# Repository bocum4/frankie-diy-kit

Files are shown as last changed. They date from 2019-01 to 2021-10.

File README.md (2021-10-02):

# frankie-diy-kit
Related hardware and building files. 

NOTA IMPORTANTE:

LIMITACIÓN DE GARANTÍA.

Este es un proyecto de dificultad media a avanzada. Se sugiere encarecidamente el previo conocimiento en el código de resistencias y otros elementos electrónicos así como experiencia soldando con cautín y soldadura de estaño. Bocuma no se responsabiliza por cualquier daño personal o material, defecto o malfunción derivada del incorrecto ensamble del kit.

Si tuviste problemas al armar tu kit y este no funciona después de haberlo ensamblado y verificado la guia de ensamble y guía de usuario, podremos asesorarte sin costo siempre y cuando esta revisión se realice durante los 30 días naturales siguientes a la fecha de tu compra. Transcurrido este lapso de tiempo las revisiones incurren en honorarios y están sujetas a nuestra disponibilidad y según nuestra carga de trabajo. Ponte en contacto con nosotros en contacto@bocuma.mx 

Todos nuestros kits están garantizados por nuestros proveedores, si por alguna razón algún componente de tu kit presenta una falla de fábrica lo reemplazaremos sin costo, para ello requeriremos que nos envies el componente o pieza defectuosa. Esta garantía tiene validez hasta por 3 meses después de la fecha de tu compra. Ponte en contacto con nosotros en contacto@bocuma.mx y te guiaremos en el proceso.

En caso de que a tu kit le falte una pieza o la hayas extraviado, puedes contactarnos en contacto@bocuma.mx y con gusto nos pondremos de acuerdo contigo para su reposición. Esta garantía tiene validez hasta por 3 meses después de la fecha de tu compra.

HACIA NUEVOS UNIVERSOS SONOROS | BOCUMA GDL MX 2021.

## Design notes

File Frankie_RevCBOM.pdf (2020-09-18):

Can | Valor | Designadores

SWITCHES

1 | DIP-08-PTH | MAD_SEQUENCES
8 | Switch Tactile 12mm | S1, S2, S3, S4, S5, S6, S7, S8
2 | Switch Slide | FILTER, SEQUENCER

CAPACITORES

2 | 4.7uF | C3, C5
1 | 2.2uF | C2
1 | 10uF | C7
2 | 1000pF / .001uF | C4, C6
1 | 0.22uF | C1

POTENCIOMETROS

1 | 100k (lin) | VR1
9 | 50k (lin) / 100k (lin) | F1, F2, F3, F4, F5, F6, F7, F8, PWM

RESISTENCIAS

2 | Photoresistor | R19, R20
1 | 4.7K | R14
12 | 10K | R5, R21, R22, R25, R27, R28, R29, R30, R31, R32, R33, R34
6 | 22K | R3, R8, R12, R16, R17, R26
4 | 47K | R4, R9, R13, R15
8 | 100k | R1, R2, R6, R7, R11, R23, R24, R35
1 | 390K | R18
1 | 470K | R10

CHIPS

1 | 40106N | IC6
1 | 4040N | IC7
1 | 4051N | IC8
8 | 2N3906 | Q1, Q2, Q3, Q4, Q5, Q6, Q7, Q8
5 | LM358N | IC1, IC2, IC3, IC4, IC5

HARDWARE Y OTROS MATERIALES
1 | Output jack | J1
1 | Broche bat 9V | POWER
1 | Base 14
2 | Base 16
5 | Base 8
1 | PCB Frankie

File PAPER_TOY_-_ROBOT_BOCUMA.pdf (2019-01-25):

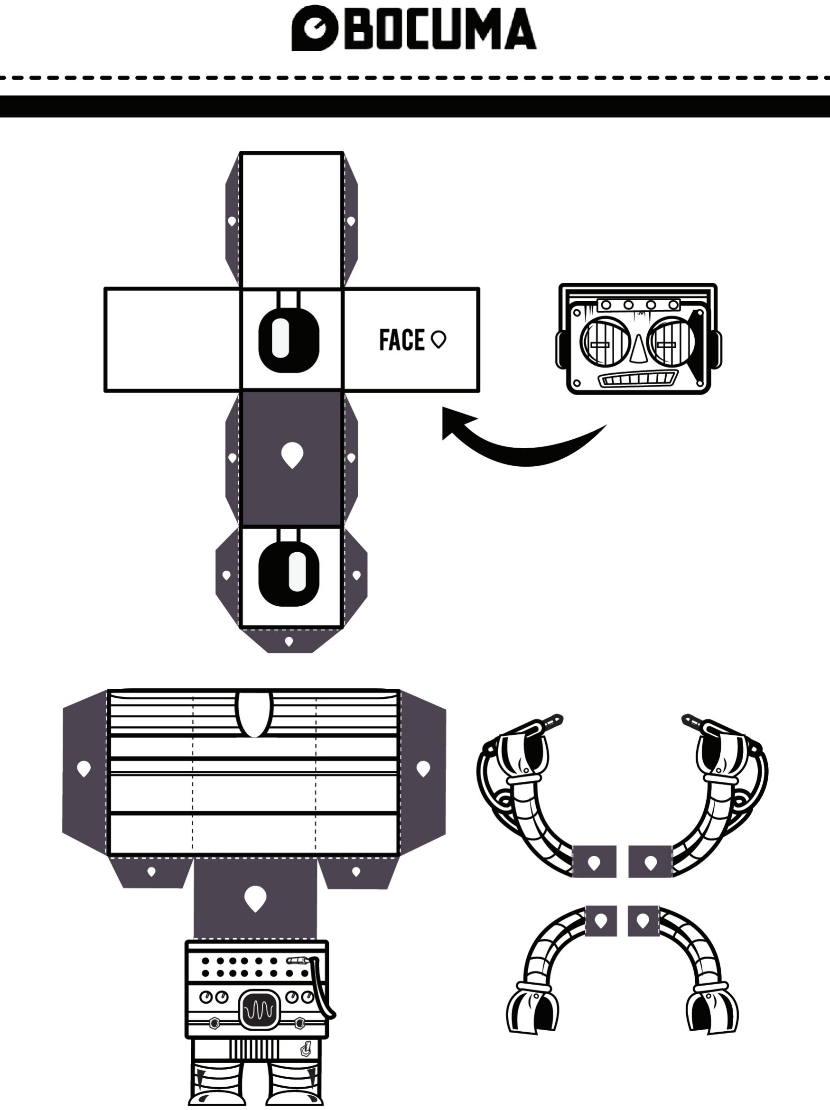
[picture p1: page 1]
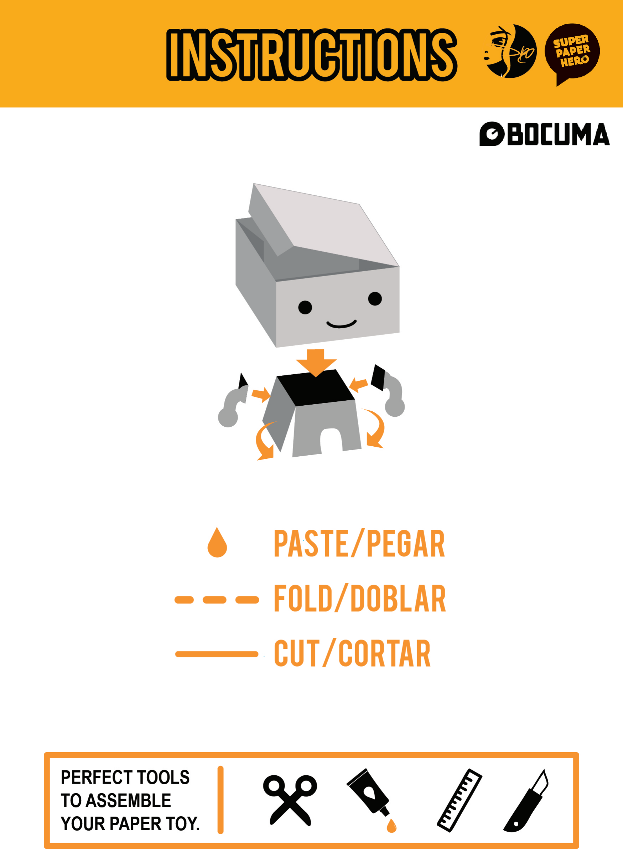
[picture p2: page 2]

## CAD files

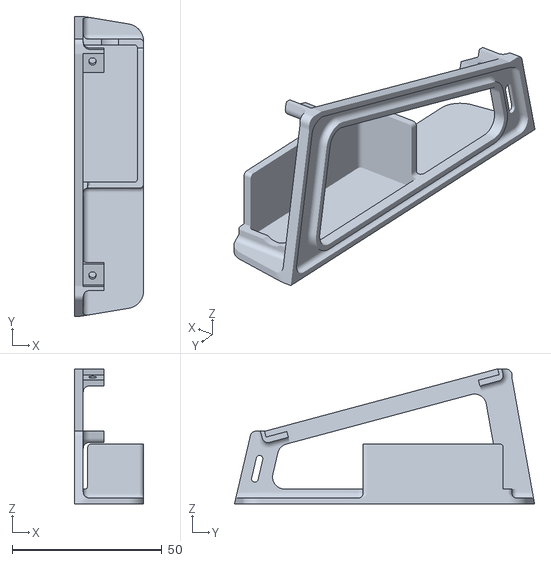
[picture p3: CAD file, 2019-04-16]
FrankieP1.stl
23.2 x 100.3 x 45.1

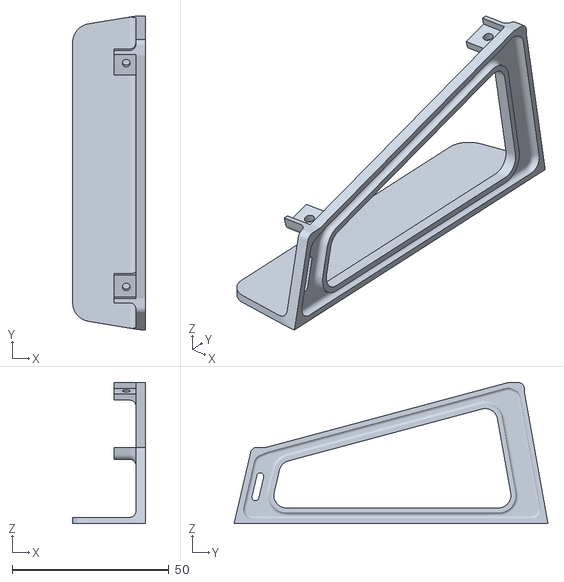
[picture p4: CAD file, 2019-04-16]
FrankieP2.stl
23.2 x 100.3 x 45.1

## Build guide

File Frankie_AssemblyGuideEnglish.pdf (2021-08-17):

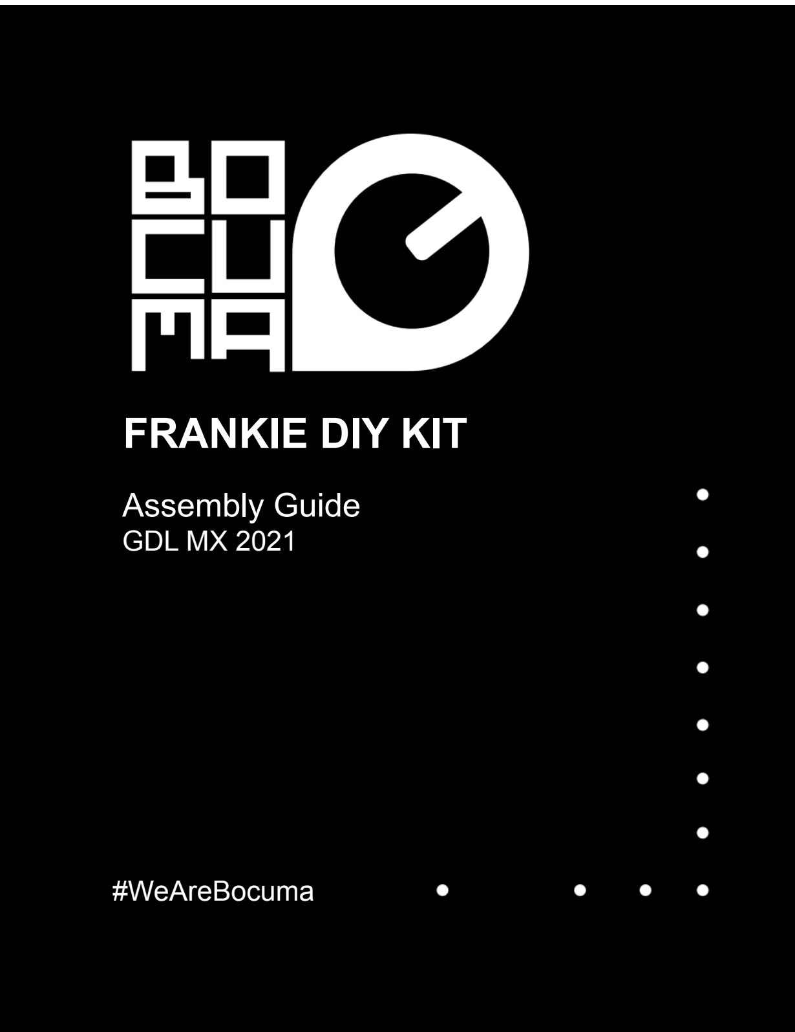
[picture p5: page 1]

# FRANKIE DIY KIT

## Assembly Guide

### GDL MX 2021

### #WeAreBocuma

## IMPORTANT NOTE

This is a medium to advanced difficulty project. Previous knowledge in the code of resistors and other electronic elements as well as experience soldering with soldering iron and tin solder is suggested. Bocuma is not responsible for any personal or material damage, defect or malfunction derived from the incorrect assembly of the kit.

TOWARDS NEW UNIVERSES OF SOUND GDL MX 2021

A few months ago, inspired by Mary Shelley's famous novel, we created Frankie. A mini beast with a sawtooth-like roar and the ability to alter his shriek with a low-pass filter, controlled by movement through the variation of light captured by a set of photoresistors.

Frankie for us was an adventure, a combination of many things learned and many things bumpy. It brought us (and still brings us) a lot of pride and we consider it as a kind of manifesto to our humble but visionary (sometimes utopian) beginnings. As in the novel, there came a point where we wanted to kill it, to stop doing it and move on to things we considered more interesting. We didn't succeed, the beast always came back, in one way or another.

At the beginning of this year, we decided to publish Frankie under a CC license and in the form of a DIY kit, because we want every individual with the necessary interest and patience to glimpse the mysteries of analog synthesis and awaken or feed his inner genius. In addition to respecting the license, we only ask that the assembly of our kit be done with passion, pride and infinite curiosity.

This is our way of giving a gift to the world.

We suggest that the user takes ownership, at least temporarily, of a clean, well-lit and well-ventilated work space. It will be necessary to gather the necessary tools and make sure to have everything ready and at hand, so that the assembly flows in a continuous and enjoyable way. For the assembly it is required:

× Pencil soldering iron, with a point in good condition. × Soldering wire as needed
× Cutting tweezers.
× Pointed tweezers.
× Desoldering and the cunning to use it very little (or not at all).

To this list we could add patience, curiosity and all those elements that make the assembly more bearable. We like to drink coffee and assemble at night. Occasional night work allows for some inspiration that also gets from the quiet and mystery of the wee hours of the morning. The above strikes us as very ad-hoc to Frankie's monstrous subject matter. As for the ears, we like to embellish the silence of the studio-workshop with good music, the selection of which we leave to the user's discretion.

It is essential to be confident with the soldering iron and to have experience in the art of soldering PTH components, as well as knowing how to identify electronic elements and resistor values.

With everything said here, assembling the kit should not present any mishap and we hope that the user enjoys assembling it as much as we enjoyed the process of designing it.

## BOM AND PCB

Before starting, we will have to familiarize ourselves with the necessary components for the assembly, it will be necessary to review the BOM (bill of materials) in the following link:
- click here- (https://github.com/bocum4/frankie-diy-kit)Next we must familiarize ourselves with the PCB layout (electronic board):

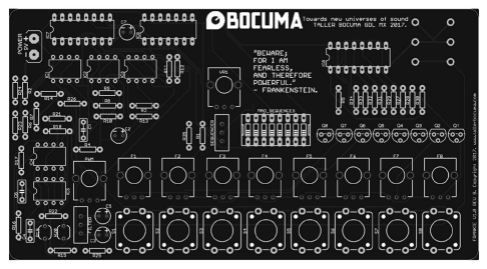
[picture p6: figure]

Each component on the board has its identifier and corresponding silhouette printed on it. All elements (with the exception of the audio output connector) are positioned on this side of the PCB.

## ASSEMBLY

Without further ado.
We begin by inspecting the electronic board to

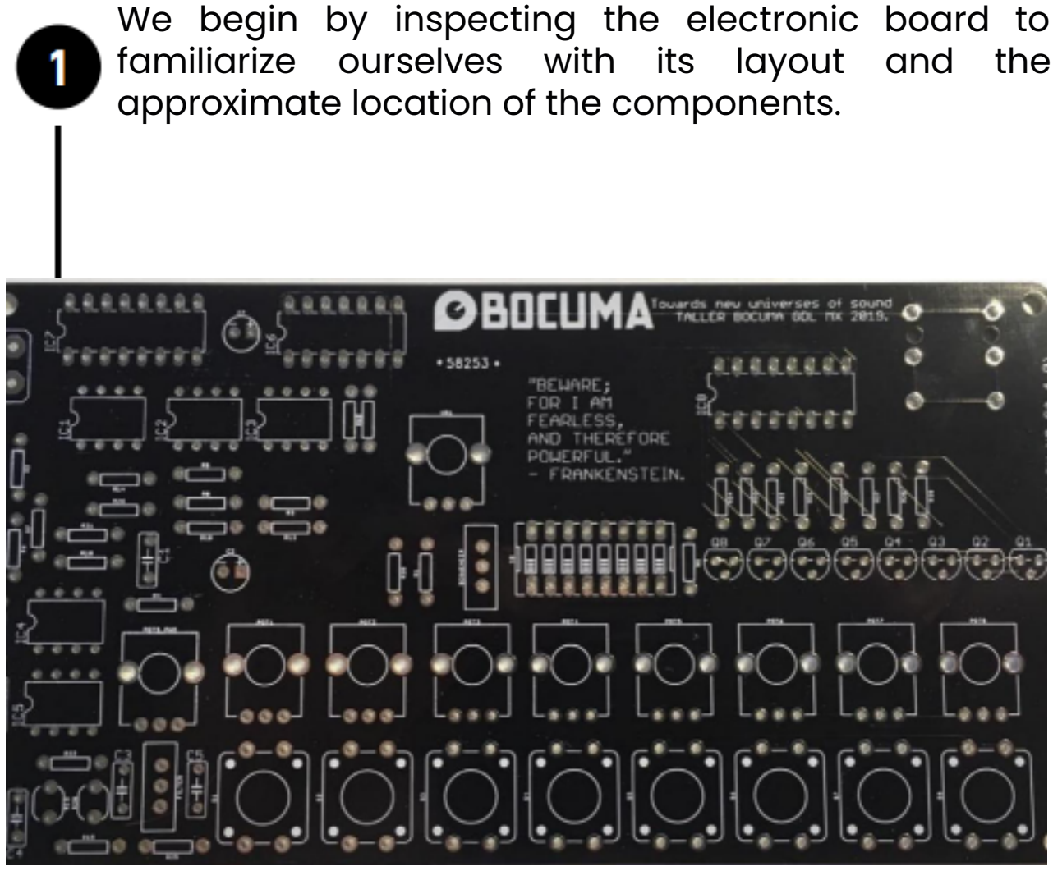
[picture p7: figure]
approximate location of the components.

familiarize ourselves with its layout and the

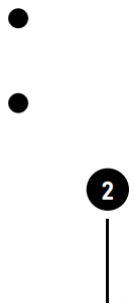
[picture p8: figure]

We start by soldering the resistors, referring to their value on the parts list value in the parts list and finding the location of each one on the board:

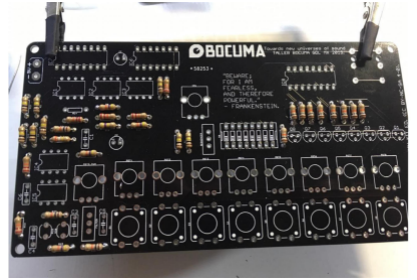
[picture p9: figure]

In the case of resistors, they do not have polarity, so it does not matter which way they are soldered. However, we must pay attention to their color code and place the indicated values in the corresponding place.

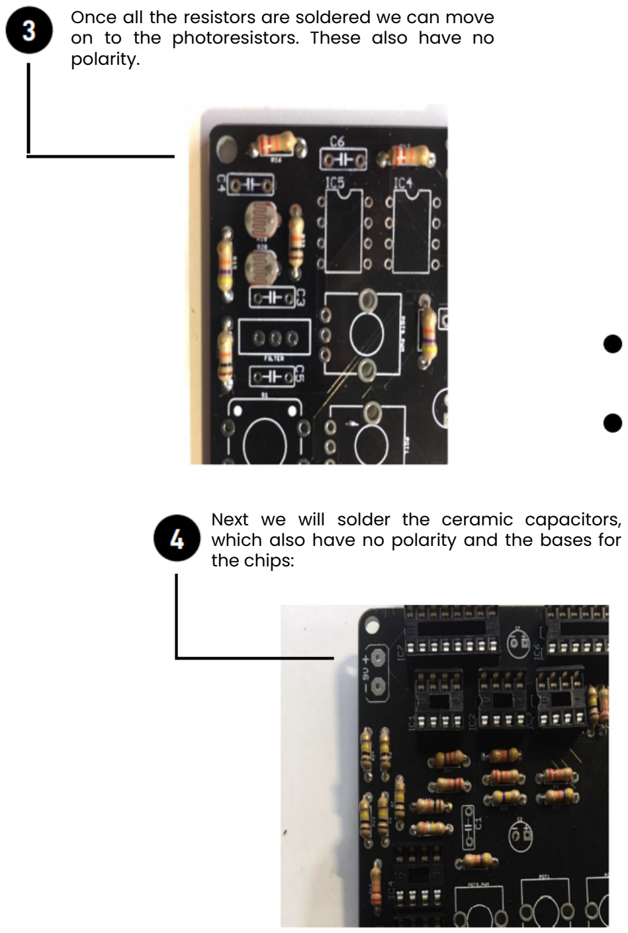
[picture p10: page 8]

Once all the resistors are soldered we can move on to the photoresistors. These also have no polarity.

Next we will solder the ceramic capacitors, which also have no polarity and the bases for the chips:

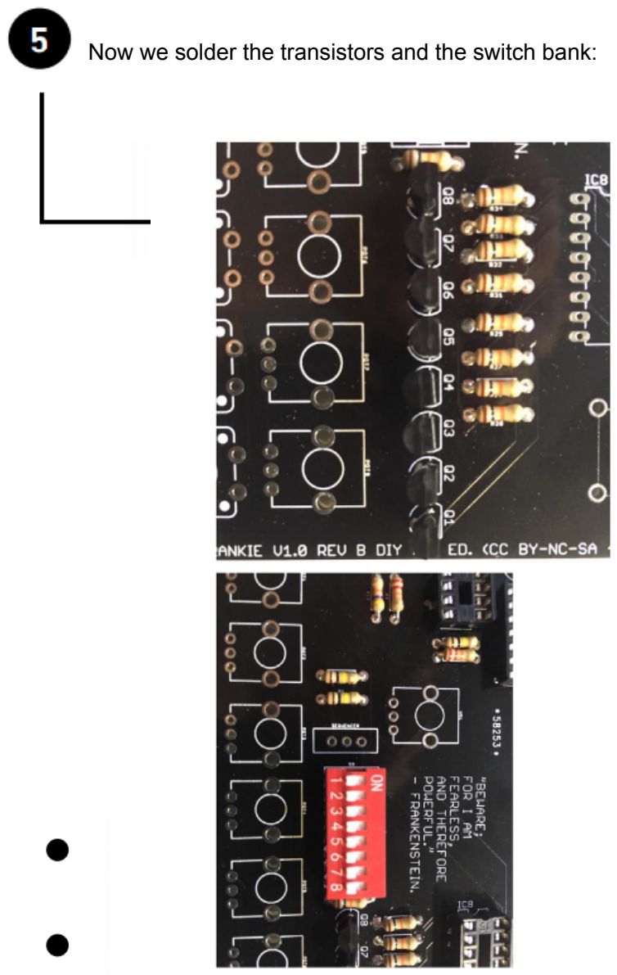
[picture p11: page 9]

5

Now we solder the transistors and the switch bank:

We continue with the electrolytic capacitors paying close attention to their POLARITY and their value, remembering that the gray stripe on the capacitor must go in the hole marked with a negative symbol (-).

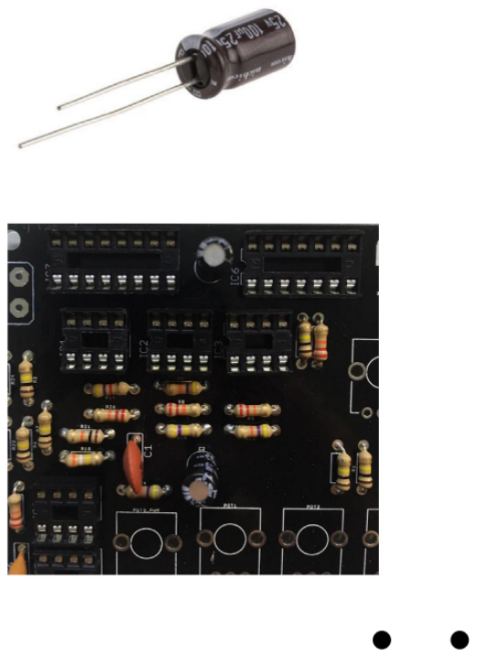
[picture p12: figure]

Now we will take care of the pulse buttons and the sequencer and filter switches:

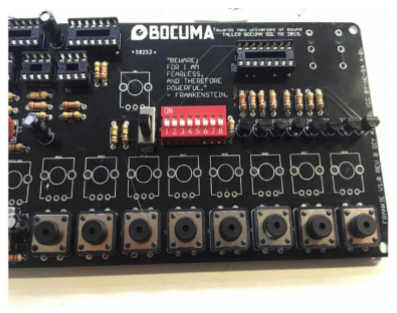
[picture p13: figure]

For the sequencer switches and the filter, we will have to cut the two end plates with tweezers.

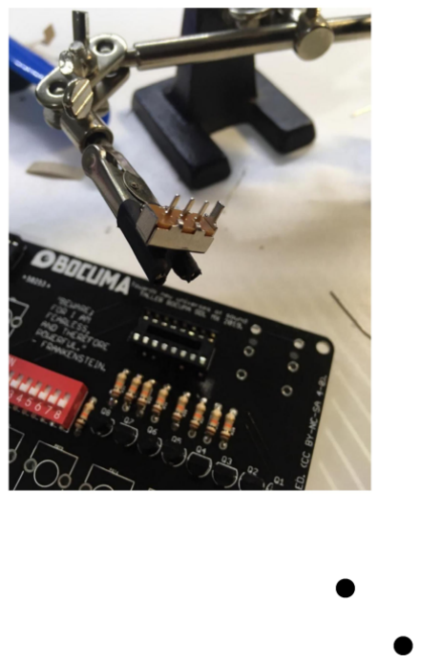
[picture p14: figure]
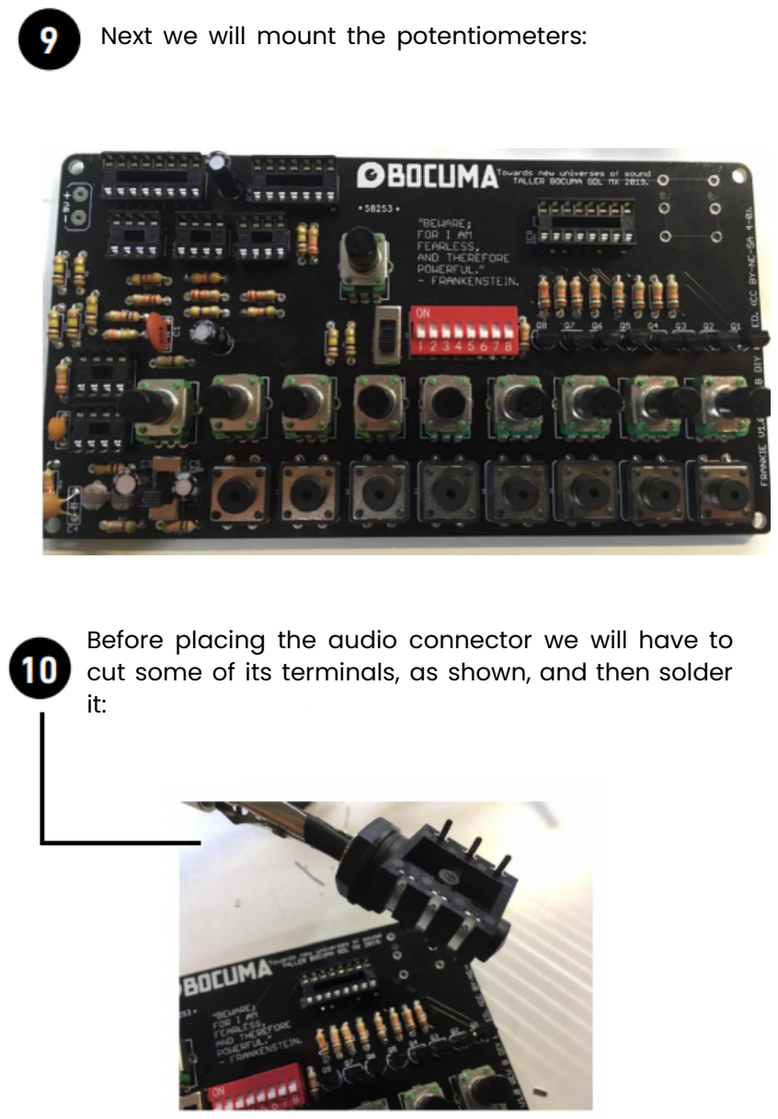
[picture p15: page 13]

Next we will mount the potentiometers:ll mount

### the potentiometers:

Before placing the audio connector we will have to cut some of its terminals, as shown, and then solder it:

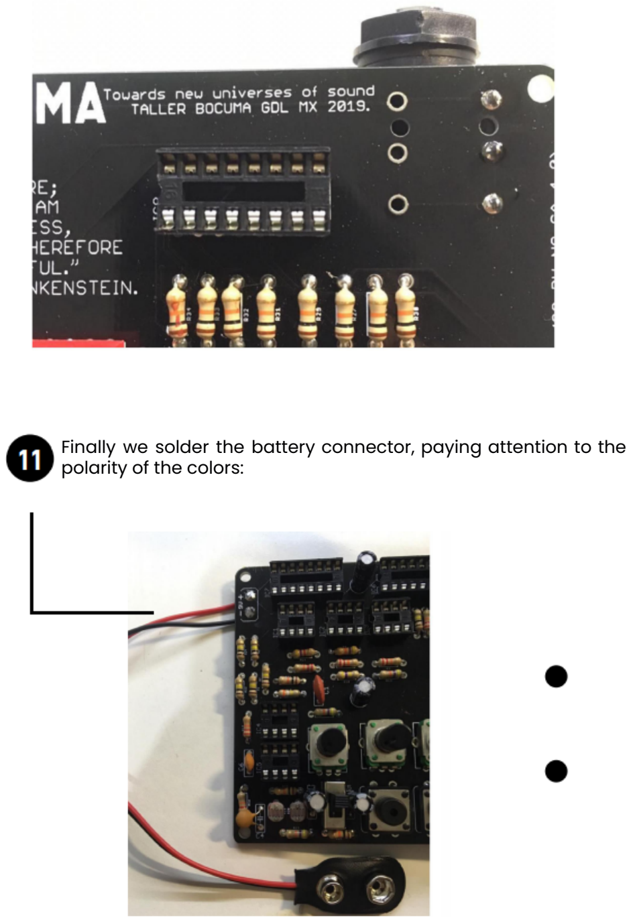
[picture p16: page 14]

Fin

ally

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
## ¿IS IT ALIVE?

To make Frankie emit his first roars, you only need to connect a 9V battery, we recommend buying a rechargeable battery to save the economy and the planet. It would be a good idea to consult the instructions here:

click here (https://github.com/bocum4/frankie-diy-kit)

DALE CLICK

## Assembly Guide

## GDL MX 2021

## #WeAreBocuma

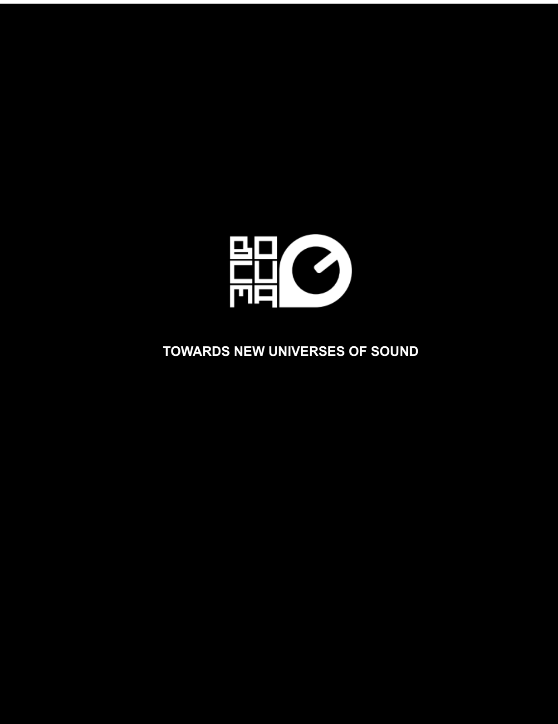
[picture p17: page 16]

TOWARDS NEW UNIVERSES OF SOUND

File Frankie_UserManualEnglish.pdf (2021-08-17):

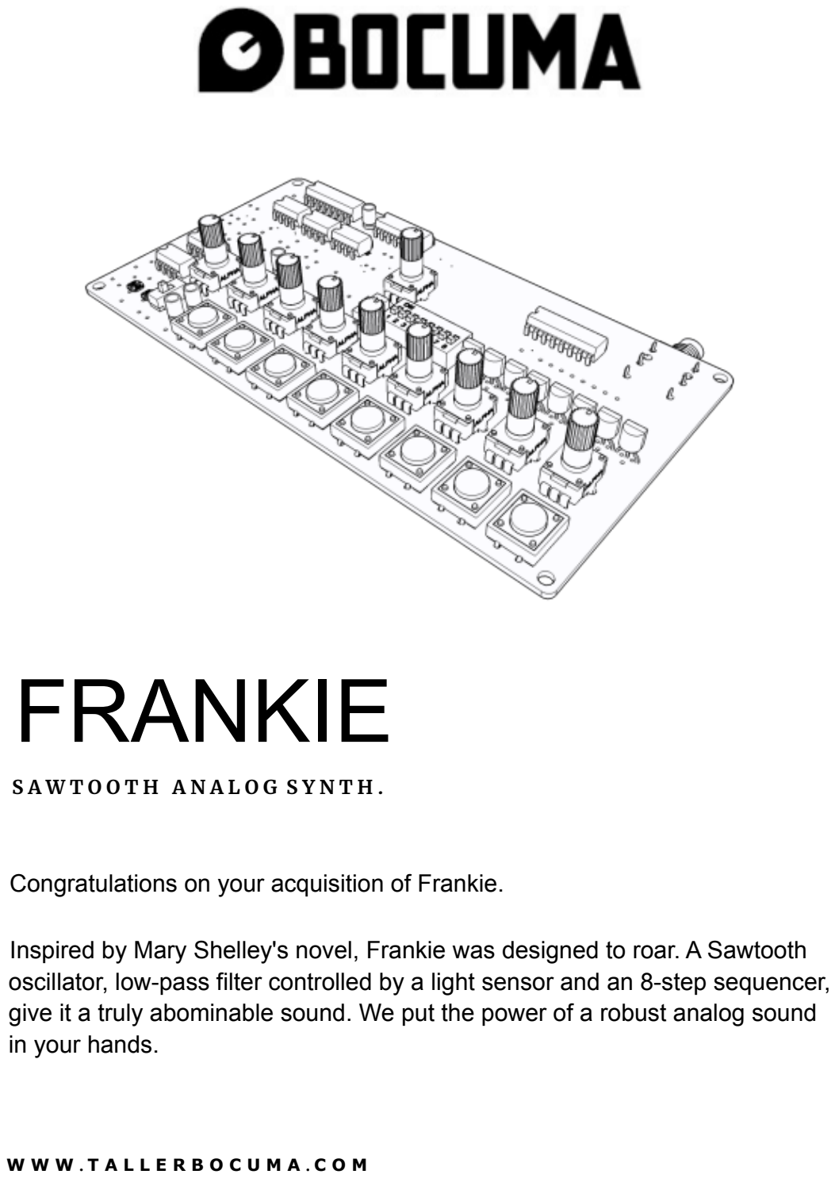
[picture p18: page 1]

# FRANKIE

S A W T O O T H A N A L O G S Y N T H .

Congratulations on your acquisition of Frankie.

### Inspired by Mary Shelley's novel, Frankie was designed to roar. A Sawtooth

oscillator, low-pass filter controlled by a light sensor and an 8-step sequencer,

### give it a truly abominable sound. We put the power of a robust analog sound

in your hands.

W W W . T A L L E R B O C U M A . C O M

D I S T R I B U T I O N O F T H E C O M P O N E N T S:

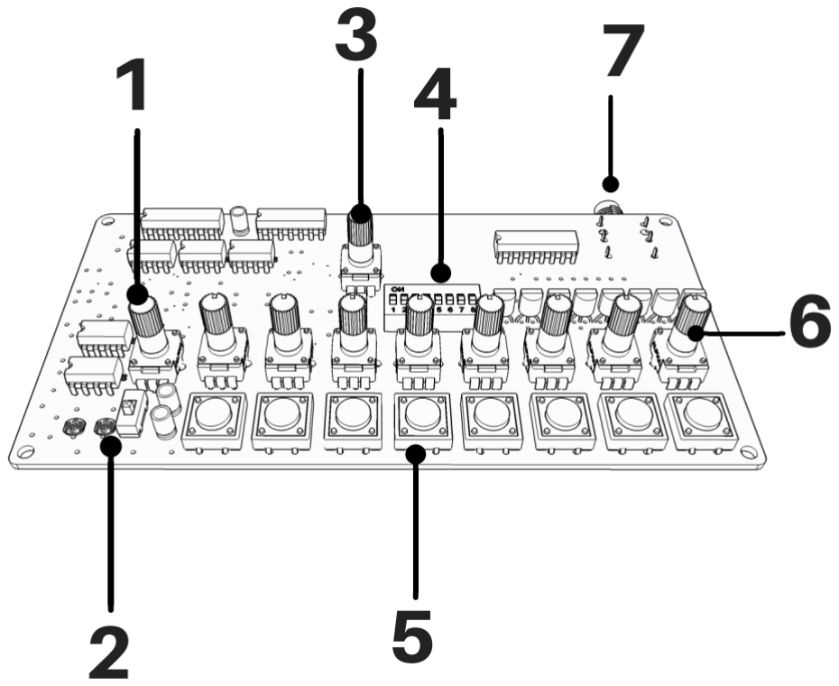
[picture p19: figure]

1. Pitch adjustment (PWM).
2. Switch and filter sensor.
3. Switch and sequencer rate (the switch is under the knob).
4. Sequence bank.
5. Note buttons (trigger).
6. Note setting (frequency).
7. Audio output.

M A N U A L O P E R A T I O N (S E Q U E N C E R D E A C T I V A T E D):

A. Connect a 9v battery to Frankie's power connector and its audio output (7) to an amplifier.
B. Set the first three sequence bank switches (4) to the "ON" (up) position, the speed or rate knob (3) all the way to the left and the switch below it all the way down (OFF).
C. To adjust Frankie's initial frequency pitch, set the "pitch adjustment" knob (1) to halfway. This knob must be held in this position in order to generate a signal at the output. You can experiment slightly to change Frankie's overall tone.
D. Press and hold any of the eight knobs (5) and then adjust its note with the knob (6) immediately above it, until it is to your liking. Each button can be set to play a different note when pressed.
E. To activate the filter, simply turn the filter switch (2) to its ON position. The filter cutoff frequency is controlled by the light level detected in the sensor (2). While pressing a note (5), move your hand closer and further away to listen to the results.

S E Q U E N C E R O P E R A T I O N:

A. With the first 3 sequence bank switches (4) facing up (ON) , set the sequencer switch under the rate knob (3) also facing up (ON). With this setting, Frankie will play its 8 notes in a linear fashion from left to right,
B. Increase the speed of the sequence (rate) by moving the knob (3) gradually to the right.
C. To change the sequence activation order, experiment with different combinations with the sequence bank switches (4).
D. To activate the filter, simply position the filter switch (2) upwards to its ON position. The filter cutoff frequency is controlled by the light level detected in the sensor (2). While the sequences are playing, move your hand closer and further away to listen to the results.

This tutorial is only a guide for initial use, the possibilities are vast. We designed Frankie with exploration in mind and hope you enjoy your experiments as much as we enjoyed designing and assembling it.

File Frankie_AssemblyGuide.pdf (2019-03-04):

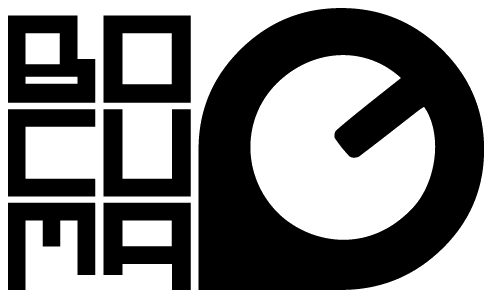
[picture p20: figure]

# FRANKIE DIY KIT

# GUÍA DE ENSAMBLE GDL MX 2019 #somosbocuma

# NOTA IMPORTANTE:

Este es un proyecto de dificultad media a avanzada. Se sugiere el previo conocimiento en el código de resistencias y otros elementos electrónicos así como experiencia soldando con cautín y soldadura de estaño. Bocuma no se responsabiliza por cualquier daño personal o material, defecto o malfunción derivada del incorrecto ensamble del kit.

HACIA NUEVOS UNIVERSOS SONOROS | BOCUMA GDL MX 2019.

# INTRO

Hace algunos meses, inspirandonos en la famosa novela de Mary Shelley, creamos a Frankie. Una mini bestia con rugido a tono diente de sierra y la capacidad de alterar su alarido con un filtro pasa-bajas, controlado por movimiento mediante la variación de luz captada por un conjunto de fotorresistores.

Frankie para nosotros fue una aventura, una combinación de muchas cosas aprendidas y muchas otras accidentadas. Nos trajo (y trae aún) mucho orgullo y lo consideramos como una especie de manifesto a nuestros humildes pero visionarios (a veces utópicos) inicios. Al igual que en la novela, llegó el punto donde quisimos matarlo, dejar de hacerlo y pasar a cosas que considerábamos más interesantes. No lo logramos, la bestia siempre volvió, de alguna manera u otra.

A inicios de este año, decidimos publicar a Frankie bajo una licencia CC y en forma de kit DIY, por que queremos que todo individuo con el interés y la paciencia necesaria, pueda vislumbrar los misterios de la sintesis analogica y despierte o alimente a su genio interior. Además del respeto a la licencia, solo pedimos que el ensamble de nuestro kit se realice con pasión, orgullo e infinita curiosidad.

Esta es nuestra manera de darle un regalo al mundo.

# ANTES DE COMENZAR

Sugerimos que el usuario se apropie, al menos de manera temporal, de un espacio de trabajo limpio, bien iluminado y bien ventilado. Habrá que reunir las herramientas necesarias y asegurarse de tener todo listo y a la mano, de tal manera que el ensamble fluya de manera continua y disfrutable. Para el ensamble se requiere:

- Cautín de lapíz, con una punta en buen estado.
- Soldadura al gusto.
- Pinzas de corte.
- Pinzas de punta.
- Desoldador y la astucia para usarlo muy poco (o nada).

A esta lista podríamos añadir la paciencia, la curiosidad y todos aquellos elementos que hagan del ensamble más llevadero. A nosotros nos gusta beber café y ensamblar durante la noche. El ocasional trabajo noctámbulo permite cierta inspiración que solo obtenemos de la tranquilidad y misterio de las altas horas de la madrugada. Lo anterior nos parece muy ad-hoc a la monstruosa temática de Frankie. En cuanto a las orejas, nos gusta adornar el silencio del estudio-taller con buena música cuya selección dejaremos al criterio del usuario.

Es esencial tener confianza en la maniobra del cautín y contar con experiencia en el arte de la soldadura con estaño para componentes PTH, así como saber identificar elementos electrónicos y valores de resistencias.

Con todo lo dicho aquí, ensamblar el kit no debe presentar ningún percance y esperamos que el usuario disfrute de ensamblarlo tanto como nosotros disfrutamos el proceso de diseñarlo.

# BOM Y PCB

Antes de comenzar, tendremos que familiarizarnos con los componentes necesarios para el ensamble, será necesario revisar el BOM (lista de materiales) en la siguiente
liga: | https://github.com/TBocuma/frankie-diy-kit/blob/master/Frankie_BOM.pdf | para
después identificarlos en el contenido del kit.

A continuación debemos familiarizarnos con el layout del PCB (tarjeta electrónica):

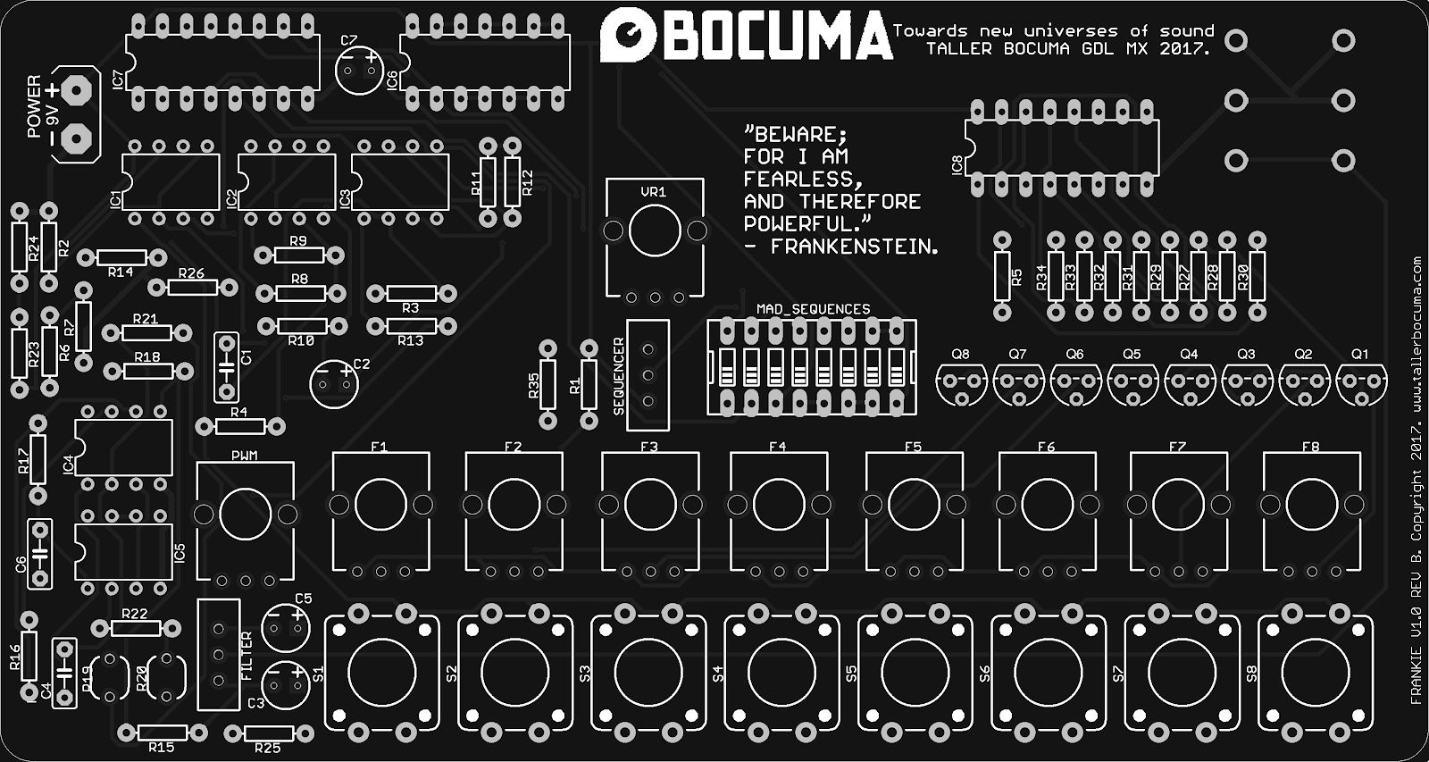
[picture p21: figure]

Cada componente en la tarjeta tiene impreso su identificador y su silueta correspondiente. Todos los elementos (a excepción del conector de salida de audio) se posicionan en esta cara del PCB.

# ENSAMBLE

Sin mayor preámbulo.

1) Iniciamos inspeccionando la tarjeta electrónica para familiarizarnos con su layout y la ubicación aproximada de los componentes.

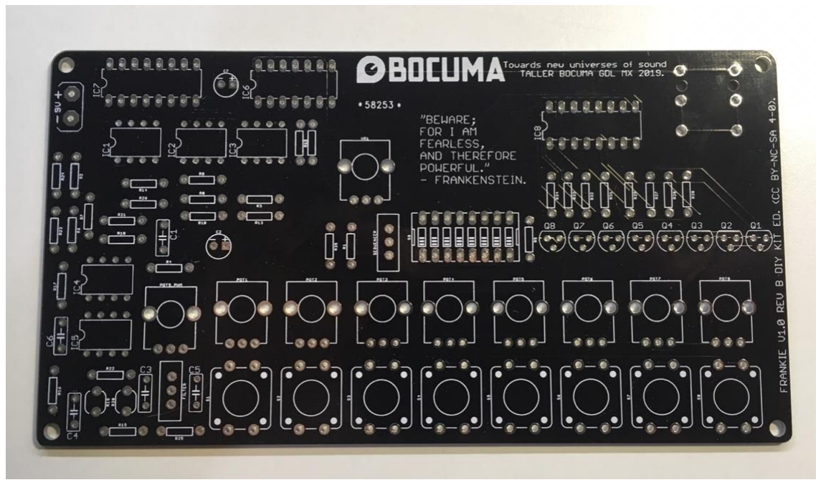
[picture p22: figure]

2) Iniciamos soldando las resistencias, refiriéndonos a su valor en la lista de partes y buscando la ubicación de cada una en la tarjeta:

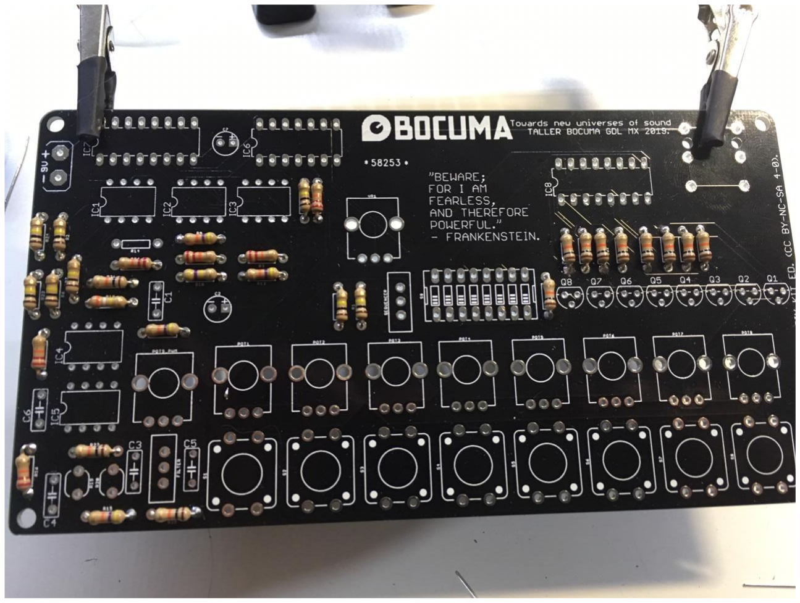
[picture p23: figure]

En el caso de las resistencias, no presentan polaridad por lo que no importa con qué orientación las soldemos. Sin embargo, hay que prestar atención a su código de colores y colocar los valores indicados en el lugar correspondiente.

3) Una vez soldadas todas las resistencias podemos pasar a los fotoresistores. Estos tampoco presentan polaridad.

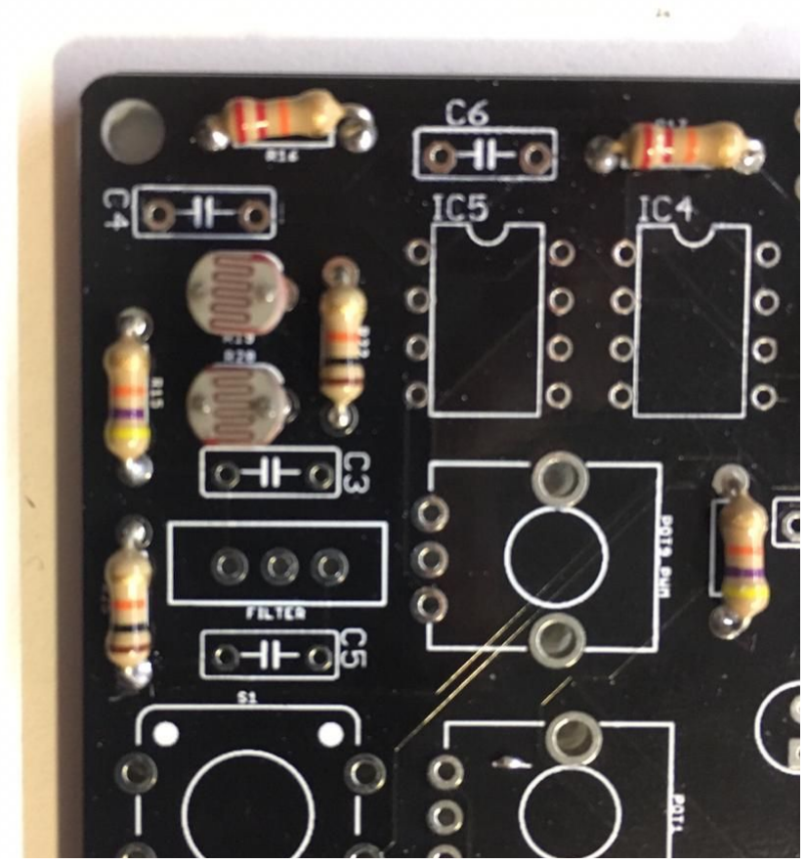
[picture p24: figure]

3) A continuación soldaremos los capacitores ceramicos, que tampoco presentan polaridad y las bases para los chips:

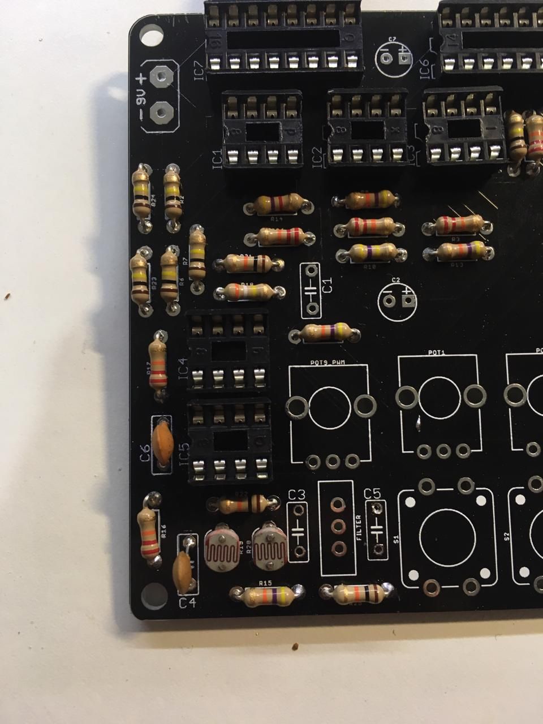
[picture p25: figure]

6) Ahora soldamos los transistores y el banco de switches:

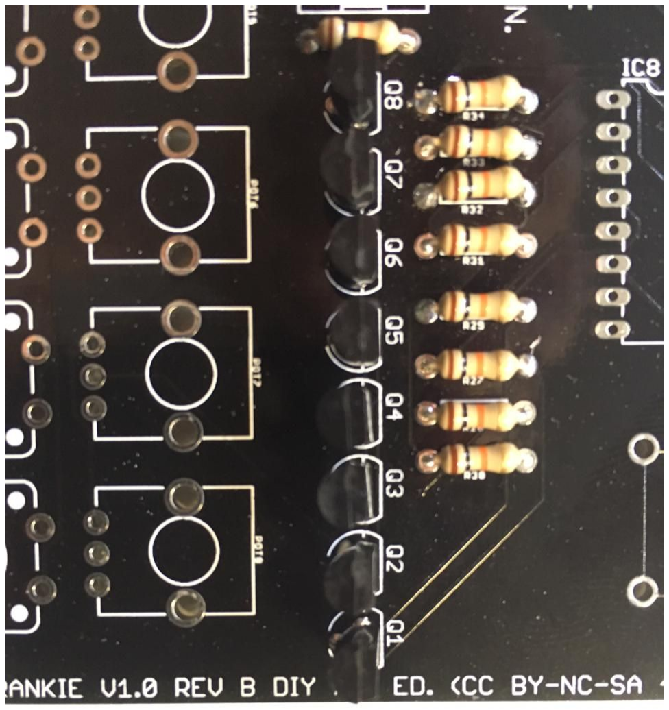
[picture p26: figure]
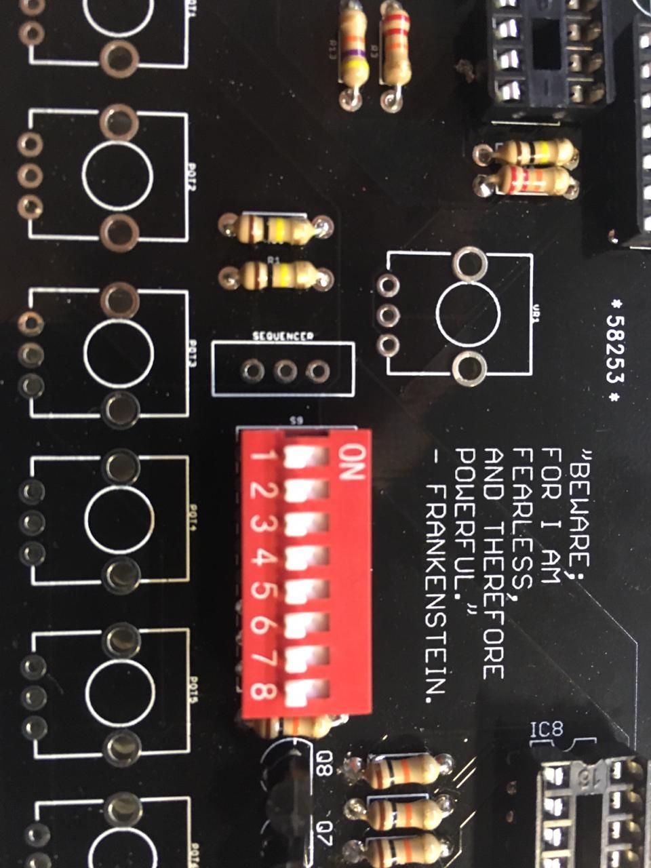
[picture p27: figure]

5) Continuamos con los capacitores electrolíticos poniendo mucha atención en su POLARIDAD y su valor, recordando que la franja gris en el capacitor debe ir en el orificio marcado con un símbolo negativo (-).

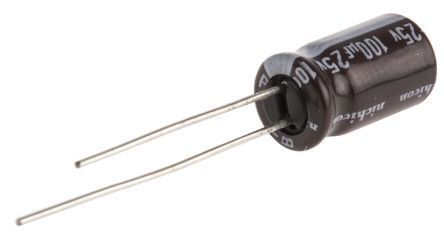
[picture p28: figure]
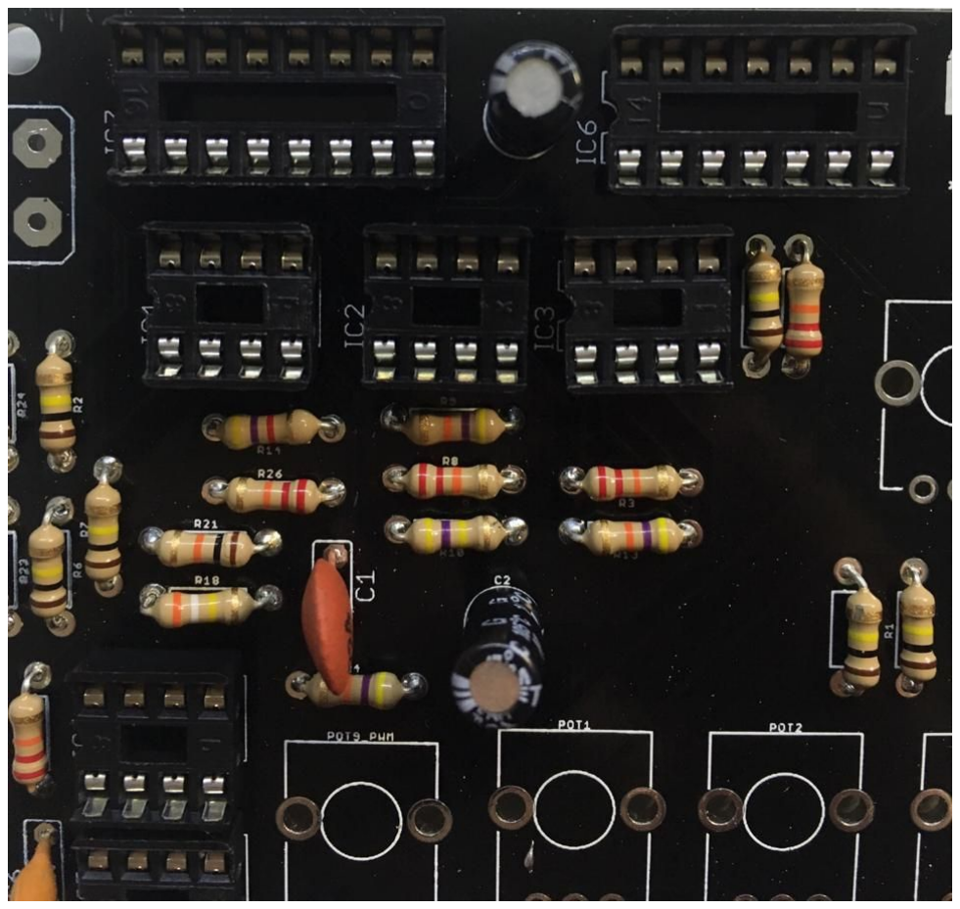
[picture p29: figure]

6) Ahora nos haremos cargo de los botones de pulso y los switches del secuenciador y el filtro:

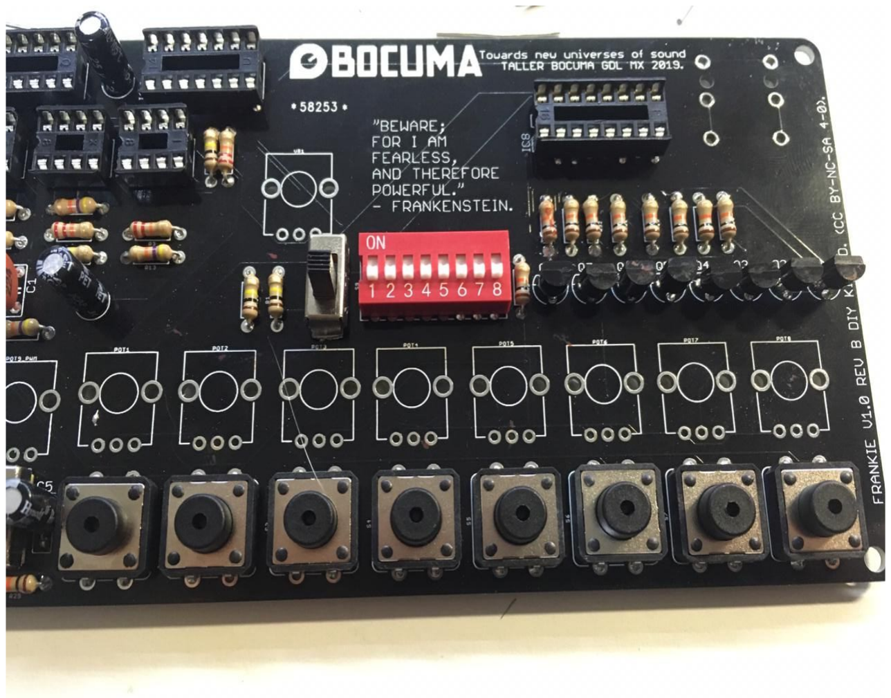
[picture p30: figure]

Para los interruptores del secuenciador y el filtro, tendremos que cortar las dos láminas de los extremos con unas pinzas.

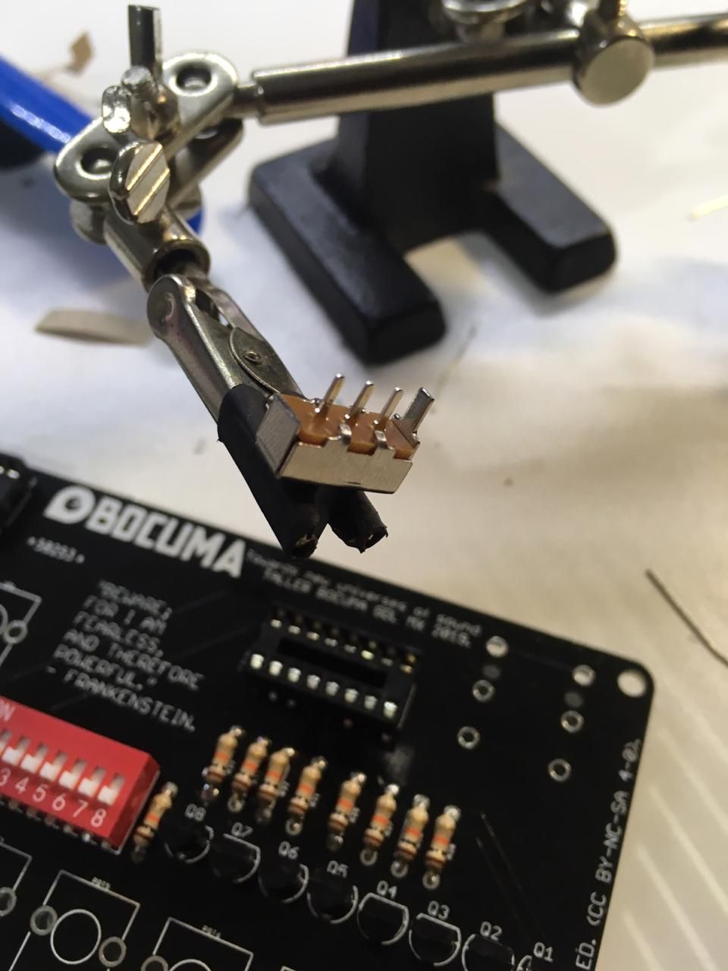
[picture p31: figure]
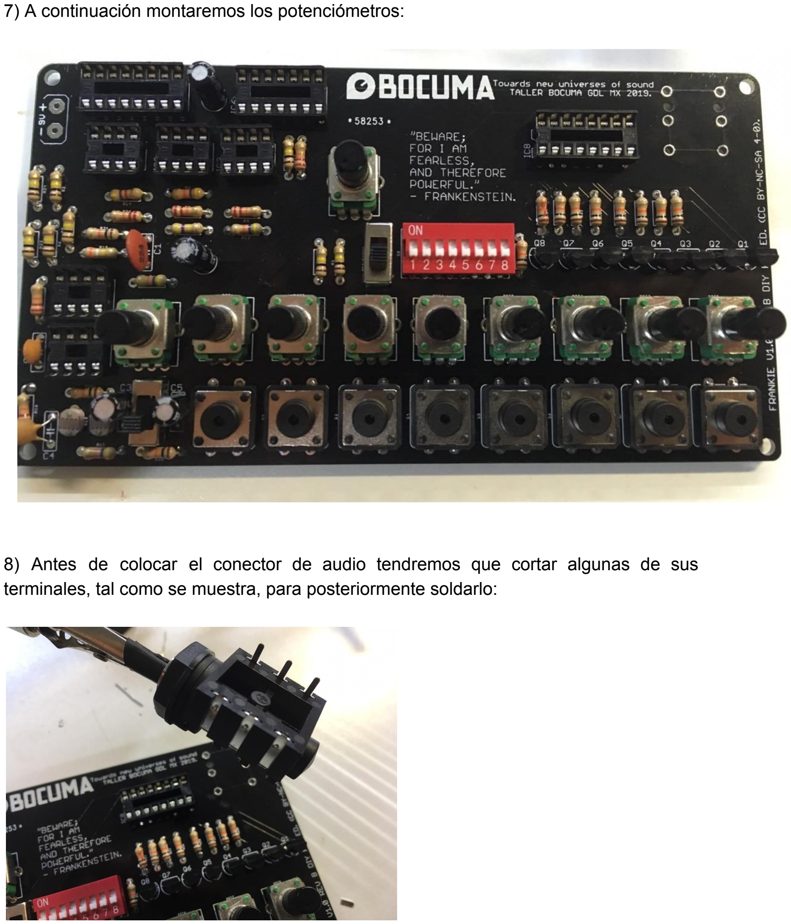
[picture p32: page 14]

7) A continuación montaremos los potenciómetros:
8) Antes de colocar el conector de audio tendremos que cortar algunas de sus terminales, tal como se muestra, para posteriormente soldarlo:

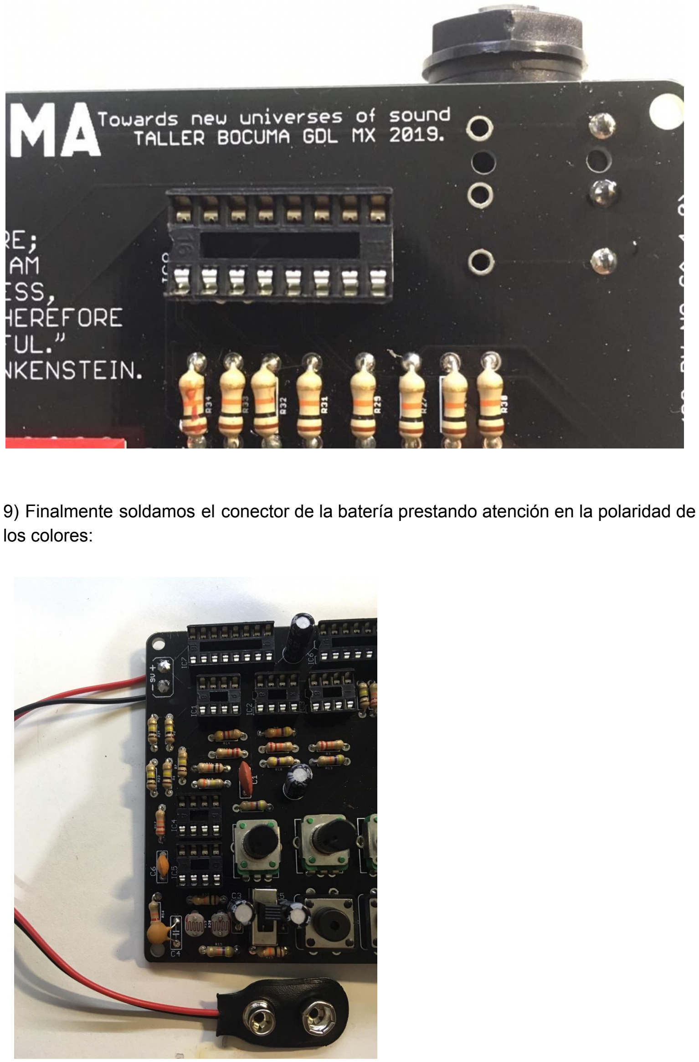
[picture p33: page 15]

9) Finalmente soldamos el conector de la batería prestando atención en la polaridad de los colores:

# ¿ESTA VIVO?

Para que Frankie emita sus primeros rugidos, solo hace falta conectarle una batería de 9V, nosotros recomendamos adquirir una batería recargable para cuidar la economía y el planeta. Vendría bien consultar el instructivo aquí:

https://github.com/TBocuma/frankie-diy-kit/blob/master/InstructivoFrankie.pdf

# #somosbocuma

Hacia nuevos universos sonoros. GDL MX.
Marzo 2019.

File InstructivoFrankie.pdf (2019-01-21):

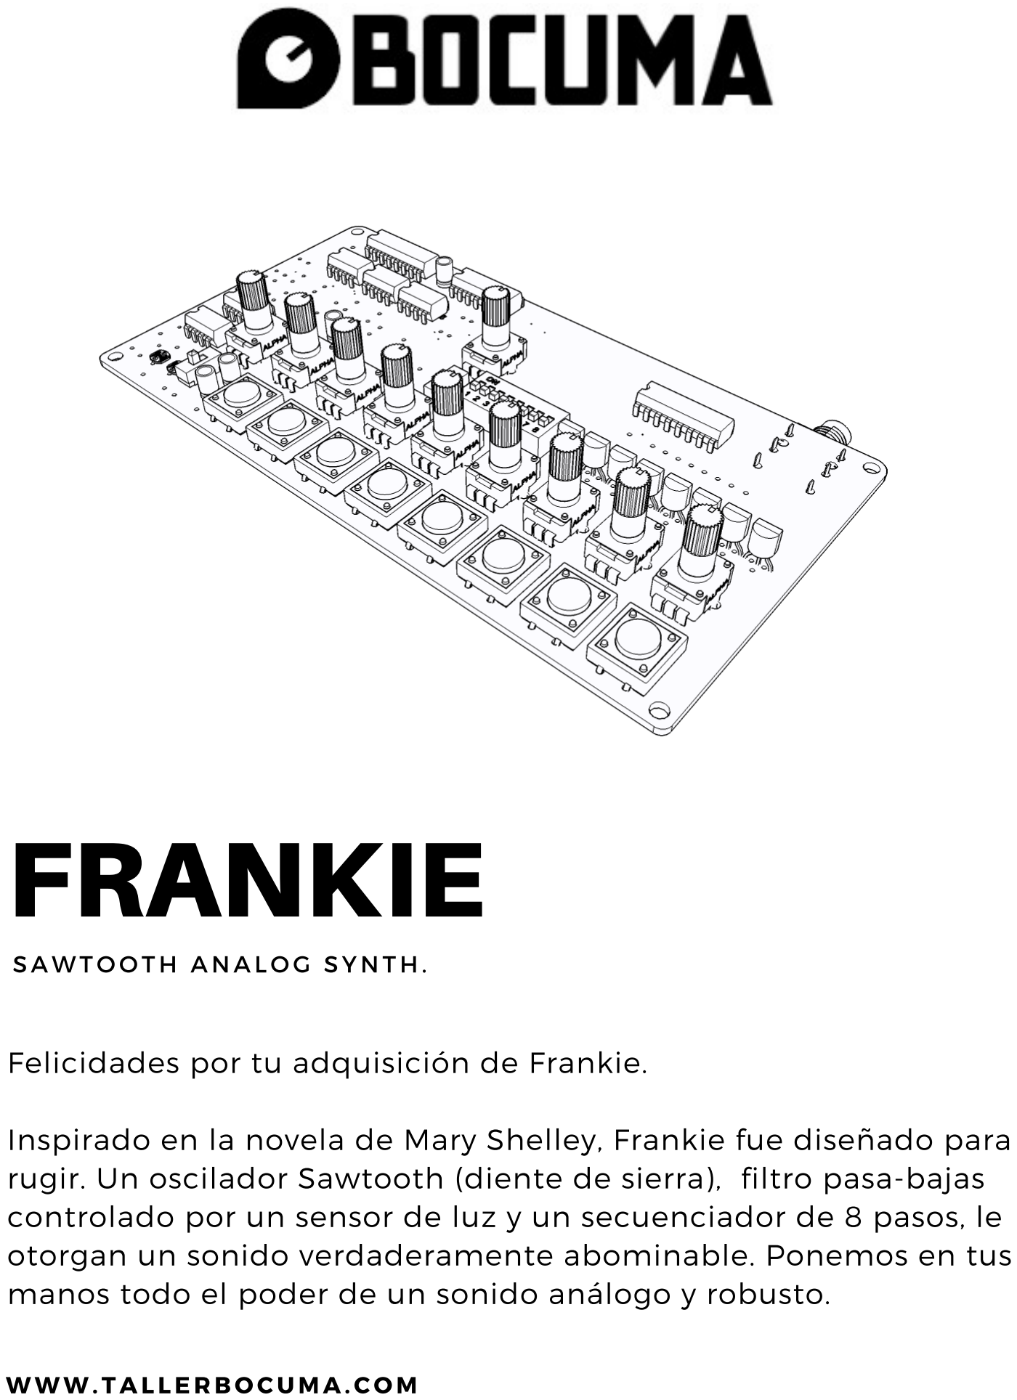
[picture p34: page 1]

S AWT O O T H A N A L O G SY N T H .

WWW. T A L LE R B O C U M A .C O M

Felicidades por tu adquisición de Frankie.

Inspirado en la novela de Mary Shelley, Frankie fue diseñado para

rugir. Un oscilador Sawtooth (diente de sierra), filtro pasa-bajas

controlado por un sensor de luz y un secuenciador de 8 pasos, le

otorgan un sonido verdaderamente abominable. Ponemos en tus

manos todo el poder de un sonido análogo y robusto.

# FRANKIE

1

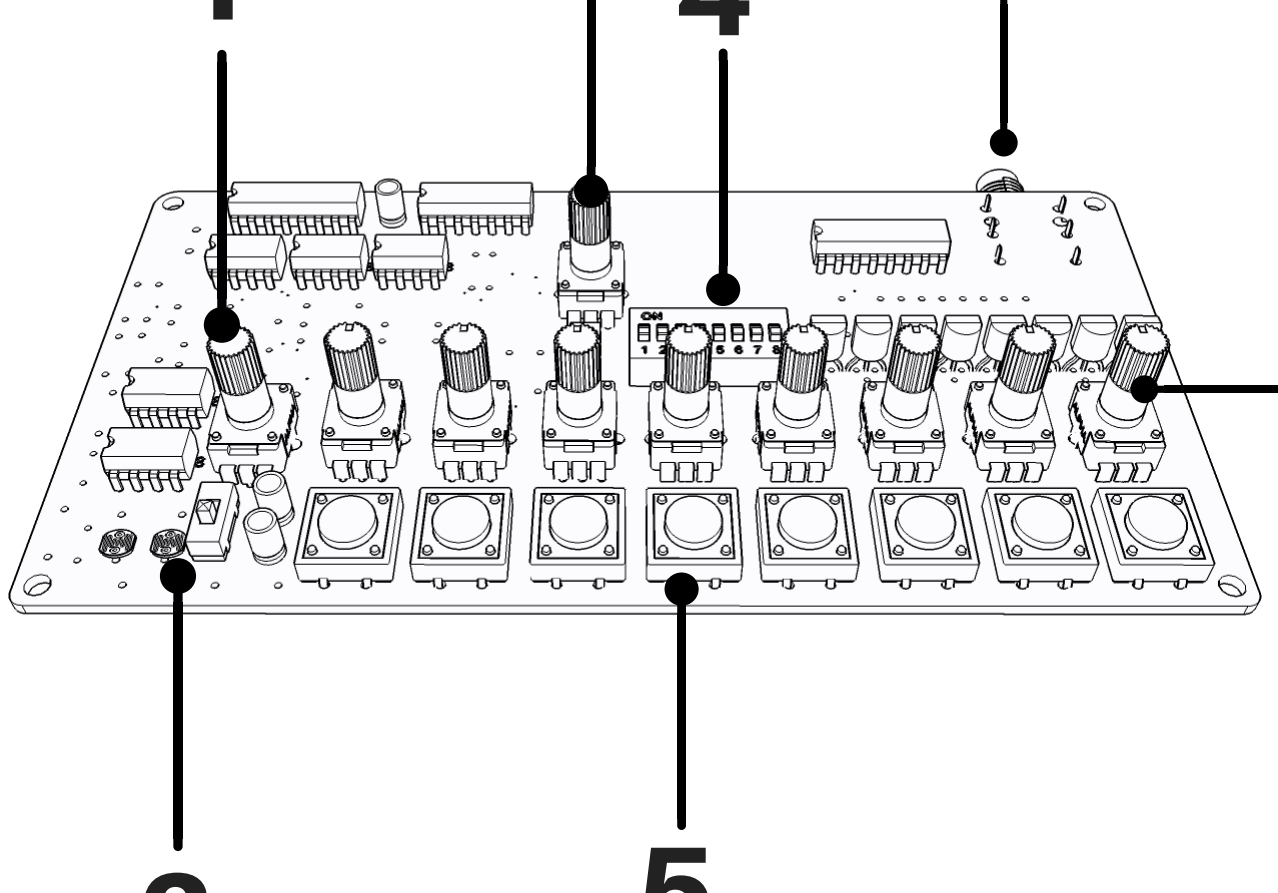
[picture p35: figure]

2

3
4

5

6

7

1. Ajuste de tono (PWM).
2. Switch y sensor del filtro.
3. Switch y velocidad (rate) del secuenciador (el switch está

debajo de la perilla).

4. Banco de secuencias.
5. Botones de nota (trigger).
6. Ajuste de nota (frecuencia).
7. Salida de Audio.

D I S T R I B U CI Ó N D E L O S C O M P O N E N TES :

O PE R A CI Ó N M A N U A L ( SEC U E N CI A D O R D ES A CT IV A D O ):

A. Conecta una batería de 9v al conector de poder de Frankie y su salida de audio
(7) a un amplificador.
B. Posiciona los tres primeros switches del banco de secuencias (4) en la posición

"ON" (arriba), la perilla de velocidad o rate (3) totalmente hacia la izquierda y el

switch debajo de esta, hacia abajo (OFF).

C. Para ajustar el tono inicial de frecuencia de Frankie, coloca la perilla de "ajuste

de tono" (1) a la mitad. Esta perilla debe mantenerse en esta posición para poder

generar una señal en la salida. Puedes experimentar ligeramente para cambiar el

tono general de Frankie.

D. Mantén presionado cualquiera de los ocho botones (5) y después ajusta su nota

con la perilla (6) inmediatamente arriba de este, hasta que sea de tu agrado. Cada

botón puede ajustarse para reproducir una nota diferente al ser presionado.

E. Para activar el filtro, simplemente posiciona el switch del filtro (2) hacia arriba, en

su posición de encendido (ON). La frecuencia de corte del filtro es controlada por el

nivel de luz detectado en el sensor (2). Mientras presionas una nota (5), acerca y

aleja tu mano para escuchar los resultados.

O PE R A CI Ó N D EL SEC U E N CI A D O R :

A. Con los primeros 3 switches del banco de secuencias (4) hacia arriba (ON) coloca

el switch del secuenciador, debajo de la perilla rate (3) también hacia arriba (ON).

Con esta configuración, frankie reproducirá sus 8 notas de manera lineal de

izquierda a derecha,

B. Incrementa la velocidad de la secuencia (rate) moviendo la perilla (3)

gradualmente hacia la derecha.

C. Para cambiar el orden de activación de la secuencia, experimenta con diferentes

combinaciones con los switches del banco de secuencias (4).

D. Para activar el filtro, simplemente posiciona el switch del filtro (2) hacia arriba,

en su posición de encendido (ON). La frecuencia de corte del filtro es controlada

por el nivel de luz detectado en el sensor (2). Mientras se reproducen las

secuencias, acerca y aleja tu mano para escuchar los resultados.

Este instructivo constituye solamente una guía de uso inicial, las

posibilidades son muy amplias. Diseñamos a Frankie con la exploración

en mente y esperamos que disfrutes tus experimentos tanto como

nosotros disfrutamos diseñarlo y ensamblarlo.

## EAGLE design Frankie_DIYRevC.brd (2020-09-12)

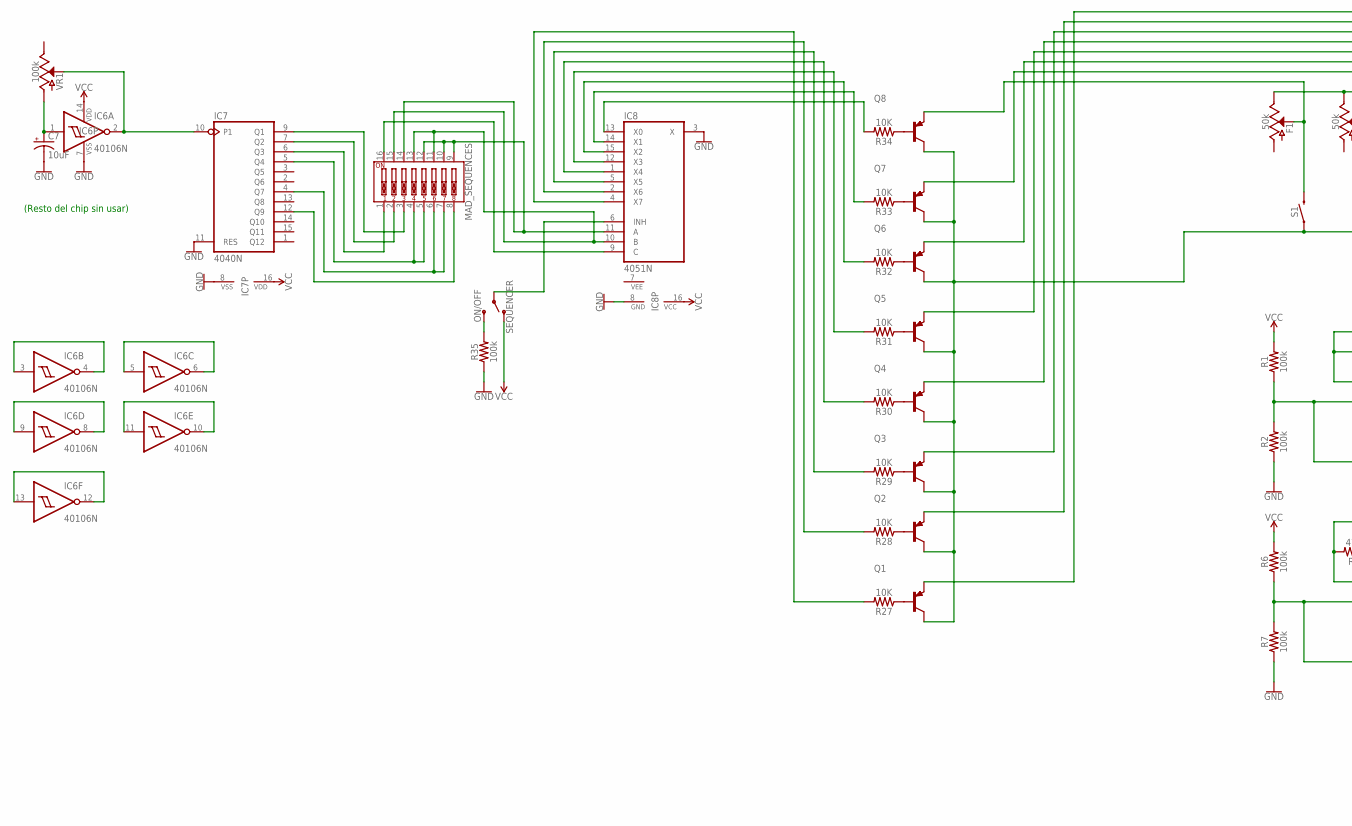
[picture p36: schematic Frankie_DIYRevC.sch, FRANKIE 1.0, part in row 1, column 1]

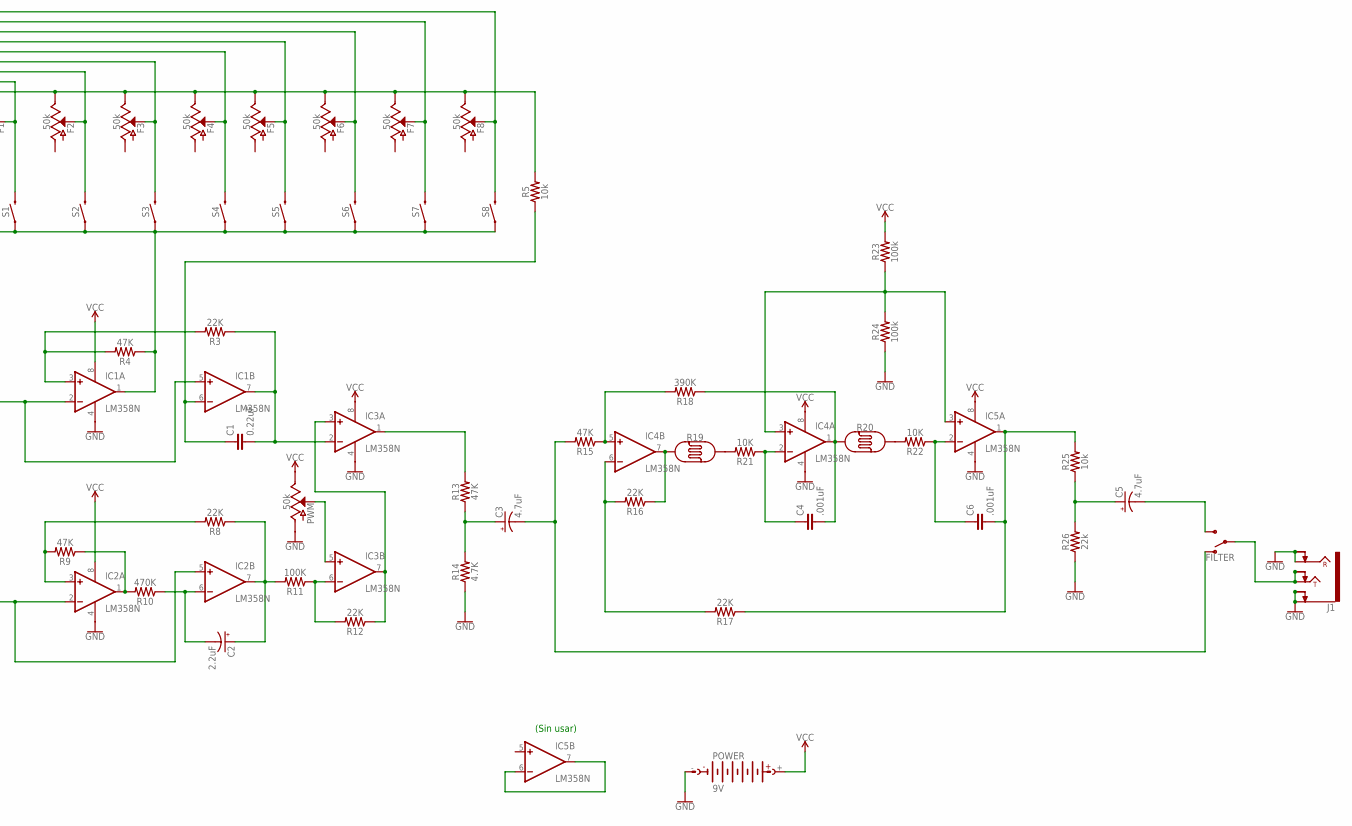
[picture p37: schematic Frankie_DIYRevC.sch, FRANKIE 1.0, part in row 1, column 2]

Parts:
C1: 0.22uF; C5B2.5
C2: 2.2uF; CPOL-RADIAL-2.5MM-5MM-KIT
C3, C5: 4.7uF; CPOL-RADIAL-2.5MM-5MM-KIT
C4, C6: .001uF; C5B2.5
C7: 10uF; CPOL-RADIAL-2.5MM-5MM-KIT
F1, F2, F3, F4, F5, F6, F7, F8: 50k; POT-PTH-ALPS-KIT
FILTER: SWITCH-SPDT-PTH-11.6X4.0MM-KIT; SWITCH_SPDT_PTH_11.6X4.0MM_KIT
IC1, IC2, IC3, IC4, IC5: LM358N; DIL08
IC6: 40106N; DIL14
IC7: 4040N; DIL16
IC8: 4051N; DIL16
J1: AUDIO_JACK_TRS_0.25"_PTH_RA; AUDIO_JACK_0.25"_TRS_PTH_RA
MAD_SEQUENCES: DIP-08-PTH; DIPSWITCH-08
POWER: 9V; AB9V
PWM: 50k; POT-PTH-ALPS-KIT
Q1, Q2, Q3, Q4, Q5, Q6, Q7, Q8: 2N3906; TO92
R1, R2, R6, R7, R23, R24, R35: 100k; AXIAL-0.3
R3, R8, R12, R16, R17: 22K; AXIAL-0.3
R4, R9, R13, R15: 47K; AXIAL-0.3
R5, R25: 10k; AXIAL-0.3
R10: 470K; AXIAL-0.3
R11: 100K; AXIAL-0.3
R14: 4.7K; AXIAL-0.3
R18: 390K; AXIAL-0.3
R19, R20: PHOTOCELLPTH-KIT; PHOTOCELL-KIT
R21, R22, R27, R28, R29, R30, R31, R32, R33, R34: 10K; AXIAL-0.3
R26: 22k; AXIAL-0.3
S1, S2, S3, S4, S5, S6, S7, S8: MOMENTARY-SWITCH-SPST-PTH-12MM; TACTILE_SWITCH_PTH_12MM
SEQUENCER: ON/OFF; SWITCH_SPDT_PTH_11.6X4.0MM_KIT
VR1: 100k; POT-PTH-ALPS-KIT

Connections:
GND: C7.2 (-), IC1.4 (V-), IC2.4 (V-), IC3.4 (V-), IC4.4 (V-), IC5.4 (V-), IC6.7 (VSS), IC7.8 (VSS), IC7.11 (RES), IC8.3 (X), IC8.8 (GND), J1.RING, J1.RING-NORM, J1.SLEEVE (EARTH), J1.SLEEVE-NORM (EARTH-NORM), POWER.-, PWM.P$3 (A), R2.P$1 (1), R7.P$1 (1), R14.P$1 (1), R24.P$1 (1), R26.P$1 (1), R35.P$1 (1)
unnamed: IC1.2 (-IN), IC1.5 (+IN), R1.P$1 (1), R2.P$2 (2)
unnamed: C1.2, IC1.7 (OUT), IC3.2 (-IN), R3.P$1 (1)
unnamed: IC1.3 (+IN), R3.P$2 (2), R4.P$2 (2)
unnamed: C1.1, IC1.6 (-IN), R5.P$1 (1)
unnamed: IC1.1 (OUT), Q1.1 (C), Q2.1 (C), Q3.1 (C), Q4.1 (C), Q5.1 (C), Q6.1 (C), Q7.1 (C), Q8.1 (C), R4.P$1 (1), S1.1, S2.1, S3.1, S4.1, S5.1, S6.1, S7.1, S8.1
unnamed: F1.P$2 (S), Q8.3 (E), S1.3 (2)
unnamed: F2.P$2 (S), Q7.3 (E), S2.3 (2)
unnamed: IC7.5 (Q4), MAD_SEQUENCES.4, MAD_SEQUENCES.5
unnamed: F4.P$2 (S), Q5.3 (E), S4.3 (2)
unnamed: F5.P$2 (S), Q4.3 (E), S5.3 (2)
unnamed: F6.P$2 (S), Q3.3 (E), S6.3 (2)
unnamed: F7.P$2 (S), Q2.3 (E), S7.3 (2)
unnamed: F8.P$2 (S), Q1.3 (E), S8.3 (2)
unnamed: F1.P$1 (E), F2.P$1 (E), F3.P$1 (E), F4.P$1 (E), F5.P$1 (E), F6.P$1 (E), F7.P$1 (E), F8.P$1 (E), R5.P$2 (2)
unnamed: IC2.2 (-IN), IC2.5 (+IN), R6.P$1 (1), R7.P$2 (2)
unnamed: IC2.3 (+IN), R8.P$2 (2), R9.P$2 (2)
unnamed: IC2.1 (OUT), R9.P$1 (1), R10.P$2 (2)
unnamed: C2.2 (-), IC2.6 (-IN), R10.P$1 (1)
unnamed: IC3.6 (-IN), R11.P$1 (1), R12.P$2 (2)
unnamed: C2.1 (+), IC2.7 (OUT), R8.P$1 (1), R11.P$2 (2)
unnamed: IC3.5 (+IN), PWM.P$2 (S)
unnamed: IC3.3 (+IN), IC3.7 (OUT), R12.P$1 (1)
unnamed: IC3.1 (OUT), R13.P$2 (2)
unnamed: C3.1 (+), R13.P$1 (1), R14.P$2 (2)
unnamed: IC4.5 (+IN), R15.P$1 (1), R18.P$2 (2)
unnamed: C3.2 (-), FILTER.1 (O), R15.P$2 (2)
unnamed: IC4.6 (-IN), R16.P$2 (2), R17.P$2 (2)
unnamed: IC4.7 (OUT), R16.P$1 (1), R19.1
unnamed: C6.2, IC5.1 (OUT), R17.P$1 (1), R25.P$2 (2)
unnamed: C4.2, IC4.1 (OUT), R18.P$1 (1), R20.1
unnamed: R19.2, R21.P$2 (2)
unnamed: R20.2, R22.P$2 (2)
unnamed: C4.1, IC4.2 (-IN), R21.P$1 (1)
unnamed: C6.1, IC5.2 (-IN), R22.P$1 (1)
unnamed: IC5.6 (-IN), IC5.7 (OUT)
unnamed: IC4.3 (+IN), IC5.3 (+IN), R23.P$1 (1), R24.P$2 (2)
unnamed: C5.1 (+), R25.P$1 (1), R26.P$2 (2)
unnamed: FILTER.2, J1.TIP, J1.TIP-NORM
unnamed: Q1.2 (B), R27.P$1 (1)
unnamed: C5.2 (-), FILTER.3 (S)
unnamed: Q2.2 (B), R28.P$1 (1)
unnamed: Q3.2 (B), R29.P$1 (1)
unnamed: Q4.2 (B), R30.P$1 (1)
unnamed: Q5.2 (B), R31.P$1 (1)
unnamed: Q6.2 (B), R32.P$1 (1)
unnamed: Q7.2 (B), R33.P$1 (1)
unnamed: Q8.2 (B), R34.P$1 (1)
unnamed: C7.1 (+), IC6.1 (I), VR1.P$3 (A)
unnamed: IC6.2 (O), IC7.10 (P1), VR1.P$2 (S)
unnamed: IC7.9 (Q1), MAD_SEQUENCES.3
unnamed: IC7.12 (Q9), MAD_SEQUENCES.8
unnamed: IC7.6 (Q3), MAD_SEQUENCES.1
unnamed: IC8.11 (A), MAD_SEQUENCES.9, MAD_SEQUENCES.10, MAD_SEQUENCES.12, MAD_SEQUENCES.14
unnamed: IC8.10 (B), MAD_SEQUENCES.11, MAD_SEQUENCES.13, MAD_SEQUENCES.15
unnamed: IC8.9 (C), MAD_SEQUENCES.16
unnamed: IC8.6 (INH), SEQUENCER.2
unnamed: R35.P$2 (2), SEQUENCER.3 (S)
unnamed: IC8.13 (X0), R34.P$2 (2)
unnamed: IC8.14 (X1), R33.P$2 (2)
unnamed: IC8.15 (X2), R32.P$2 (2)
unnamed: IC8.12 (X3), R31.P$2 (2)
unnamed: IC8.1 (X4), R30.P$2 (2)
unnamed: IC8.5 (X5), R29.P$2 (2)
unnamed: IC8.2 (X6), R28.P$2 (2)
unnamed: IC8.4 (X7), R27.P$2 (2)
unnamed: IC7.7 (Q2), MAD_SEQUENCES.2
unnamed: IC7.4 (Q7), MAD_SEQUENCES.6, MAD_SEQUENCES.7
unnamed: F3.P$2 (S), Q6.3 (E), S3.3 (2)
unnamed: IC6.3 (I), IC6.4 (O)
unnamed: IC6.5 (I), IC6.6 (O)
unnamed: IC6.8 (O), IC6.9 (I)
unnamed: IC6.10 (O), IC6.11 (I)
unnamed: IC6.12 (O), IC6.13 (I)
VCC: IC1.8 (V+), IC2.8 (V+), IC3.8 (V+), IC4.8 (V+), IC5.8 (V+), IC6.14 (VDD), IC7.16 (VDD), IC8.16 (VCC), POWER.+, PWM.P$1 (E), R1.P$2 (2), R6.P$2 (2), R23.P$2 (2), SEQUENCER.1 (O)
VEE: IC8.7 (VEE)

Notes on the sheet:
(Sin usar)
(Resto del chip sin usar)

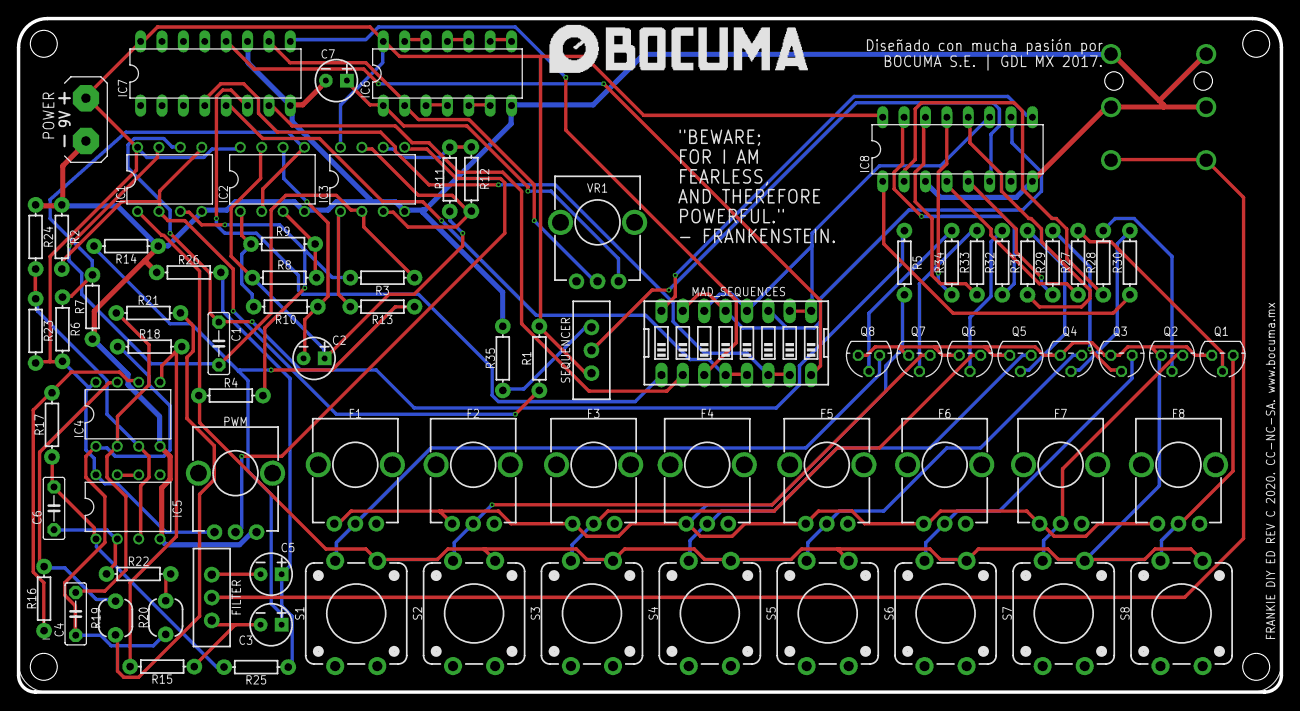
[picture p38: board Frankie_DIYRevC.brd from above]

Board: 2 copper layers, 150.0 x 80.0 mm, 81 parts (1 on the bottom side), 75 nets.

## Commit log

2019-01-21 Add Bill Of Materials.
    Added bill of materials. Frankie DIY Ed. Rev A.
2019-01-21 Add schematic in pdf format.
    Frankie DIY REV A, pdf format.
2019-01-25 Update EAGLE CAD files
    [Frankie_DIYRevB.brd, Frankie_DIYRevB.sch]
2019-03-04 Add files via upload
    Add Assembly Guide
2019-04-16 Add files via upload
    .stl files for 3D printing. Frankie Base.
    [FrankieP1.stl, FrankieP2.stl]
2020-09-12 Update EAGLE Files
    Updated EAGLE design files for REV C, Latest revision.
    [Frankie_DIYRevB.brd, Frankie_DIYRevC.brd, Frankie_DIYRevC.sch]
2020-09-16 Update BOM
    Updated bill of materials for revision C
2020-09-18 Update BOM
    Updated Rev C Bill Of Materials
2020-11-15 Upload BOM duplicate
    Uploaded BOM duplicate with different name for documentation consistency.
2020-11-24 Update Frankie_AssemblyGuide.pdf
    Uploaded updated assembly guide with branding and graphic design enhancements.
2021-08-17 Add assembly guide and user manual in English

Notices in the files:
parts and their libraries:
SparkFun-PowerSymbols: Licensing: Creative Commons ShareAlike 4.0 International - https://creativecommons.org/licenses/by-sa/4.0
